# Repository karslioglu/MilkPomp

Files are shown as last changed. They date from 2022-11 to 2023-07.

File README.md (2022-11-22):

# Milk Pomp
Proje, kullanicinin farkli tip ve hacimli bardaklara makineden süt doldurmak için kullanilacak bir cihazin kontrol kartinin tasarlanmasi işidir.

Cihazın mekanik tasarımı, flow sensör ve pompa seçimi müşteri tarafından hazırlanmıştır. Bizim yapacağımız iş ise sistemin çalışmasını sağlayacak elektronik kontrol kartının tasarlanmasıdır.

## Sistemin Çalismasi
Cihaz maksimum 9 farklı bardak bilgisini hafızada tutabilir. Kullanıcı bardak seçimi yaparak kayıtlı bardak tiplerinden birini otomatik olarak doldurabilir. Fakat istenirse kayıtlı olmayan farklı bir kabı da manuel olarak istediği miktarda doldurabilir.

Cihaz üzerinde 3 adet buton ve 1 adet 7-Segment gösterge bulunmaktadır. Ayrıca, bir pulse girişi ile **Akış Sensoru** girişi okunacak ve çıkış olarak bir role kontrol edilecektir.

	* I/O (On/Off) butonu
	* Start butonu
	* Mode butonu
	* Akış Sensoru (Encoder Pulse Input)
	* Role
	
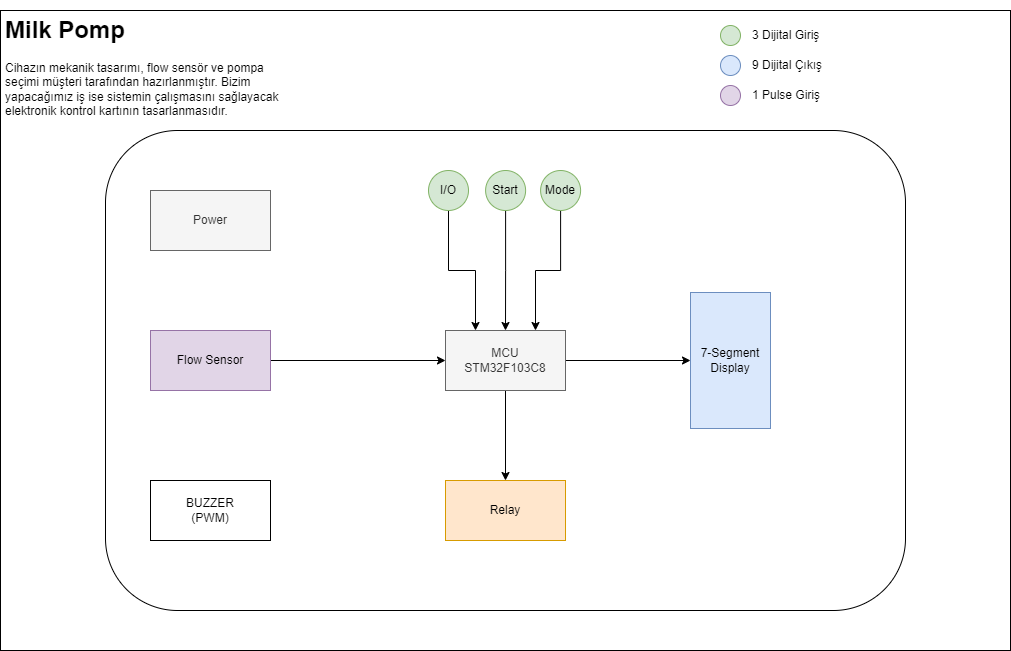
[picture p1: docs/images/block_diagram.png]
Block Diagram

	
Aşağıda tarif edilen çalışma şekilleri bu 3 buton ve gösterge kullanılarak gerçeklenecektir.

Sistemi çalıştırmak için I/O butonuna bir kere basıp bırakmak yeterlidir. Sistem kapalıyken gösterge ve diğer butonlar aktif değildir. I/O butonuna bir kere basılıp bırakıldığında sistem açılır, eğer kalibrasyon yapılmamışsa (hiç bardak tanımı yoksa) **C.** değeri görünür ve ekran yanıp söner. Aksi halde sabit olarak **0** yazar ve bardak seçimi için bekler.

Cihaz 3 farklı çalışma şekline sahip olacaktır.

### Kalibrasyon
Kalibrasyon modu, elimizde bulunan bardakların tanımlanması için kullanılır. Maksimum 9 farklı bardak tanımı yapılabilir.

Kalibrasyon modu bir adet bardak tanıtmak istenirse aşağıdaki algoritmaya göre çalışır

	1- Kalibrasyonu başlatmak için I/O butonuna 5 saniye basılı tutulur
	2- Gösterge 0 değerini gösterir ve nokta yanıp sönmeye başlar
	3- İstenilen bardak, cihazın bardak bölmesine yerleştirilir
	4- Mode butonu ile bardak seçimi yapılır (1, 2, 3, ..)
	5- Start butonuna basılı tutularak bardak doldurulur
	6- Bardak dolunca Start butonu bırakılır
	7- Start butonu bırakıldığında seçilen bardak ve doldurulan miktar bilgileri otomatik olarak kaydedilir
	8- Kalibrasyon modundan çıkmak için I/O butonuna 5 saniye bayunca basılır
	
Eğer birden fazla bardak tanımı yapılmak istenirse yukarıdaki algoritma basamaklarından 1 nolu adım ile kalibrasyon işlemi başlatılır. 2-7 adımları her bir bardak için tekrarlanır. Tüm bardakların tanımlanma işlemi bittiğinde 8 nolu adım ile kalibrasyon işlemi sonlandırılır.

Daha sonra tanımlı bir bardağın kalibrasyonu değiştirlmek istendiğinde veya yeni bir bardak tanımı yapılması gerektiğinde yukarıdaki algoritma tekrar uygulanabilir.

> Dikkat edilmesi gereken nokta, eğer bardak tanımları yapılmış bir cihazda tek bir bardağın kalibrasyonu değiştirlmek istenirse, Mode butonu ile doğru bardak numarasının seçildiğinden emin olunması gerekmektedir.

### Otomatik Mod
Kalibrasyonu yapılmış bir cihazda kullanıcı bardak seçimi yaparak tanımlı bardaklardan birini otomatik olarak doldurabilir.

	1- İstenilen bardak, cihazın bardak bölmesine yerleştirilir
	2- Mode butonu kullanılarak bardak seçimi yapılır
	3- Start butonuna basılıp bırakıldığında tanımlı miktar kadar dolum yapılır
	
Her bir bardak için yukarıdaki adımlar tekrarlanır.

### Manuel Mod
Kalibrasyon yapılarak tanımlanmamış bir bardak veya farklı bir kap doldurulmak istendiğinde Manuel mod kullanılır.

	1- Doldurulmak istenilen kap yerleştirilir.
	2- Start butonuna basılı tutulur. Butona basıldıktan 5 saniye sonra manuel dolum başlar
	3- Kullanıcı Start butonunu bıraktığında dolum işlemi sonlanır.

## Kullanilacak Bilesenler
[flow sensor](https://www.hepsiburada.com/fluidotech-kahve-makinasi-pompasi-rotary-pompa-pirinc-govdeli-p-HBV000007SB1Q)
[flow sensor kullanimi](https://how2electronics.com/iot-water-flow-meter-using-esp8266-water-flow-sensor/)
[ESP8266 with Water Flow Sensor](https://www.14core.com/wiring-esp8266-1212e-with-g12-liquid-water-flow-sensor-for-wireless-monitoring/)

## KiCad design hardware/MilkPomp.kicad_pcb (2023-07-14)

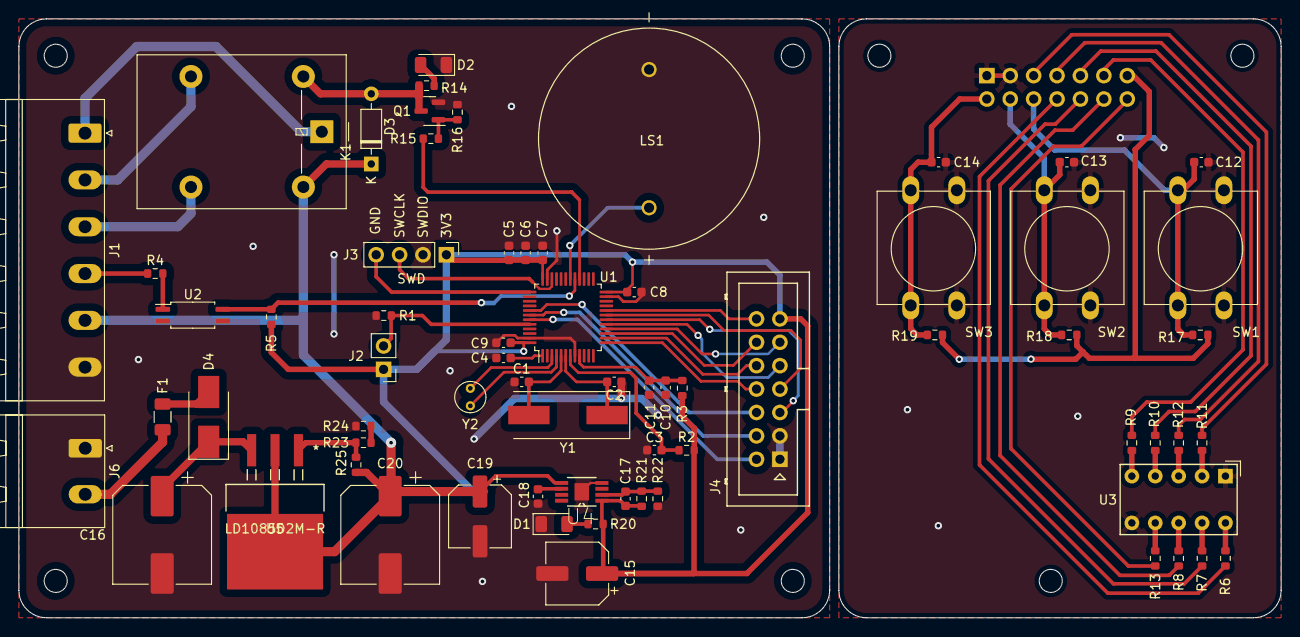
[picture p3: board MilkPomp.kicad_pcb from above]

Board: 2 copper layers, 137.0 x 65.0 mm, 76 parts (1 on the bottom side), 62 nets.

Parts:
C1, C2: 20pF; C_0603_1608Metric
C3, C5, C7, C8, C9, C10, C12, C13, C14: 100nF; C_0603_1608Metric
C4: 1uF/10V; C_0603_1608Metric
C6, C11: 1uF/6V; C_0603_1608Metric
C15: 10uF/10V; CP_Elec_6.3x7.7
C16, C20: 100uF/35V; CP_Elec_10x10.5
C17, C18: 10nF; C_0603_1608Metric
C19: 10uF/35V; CP_Elec_6.3x7.7
D1, D2: LED_GREEN; LED_1206_3216Metric
D3: 1N4148; D_DO-35_SOD27_P7.62mm_Horizontal
D4: SBR3A40SAQ; D_SMB_Handsoldering
F1: 1A; Fuse_1206_3216Metric
H1, H2, H3, H4, H5, H6, H7: MountingHole; MountingHole_2.5mm
J1: Screw_Terminal_01x06; PhoenixContact_MSTBA_2,5_6-G-5,08_1x06_P5.08mm_Horizontal
J2: BOOT; PinHeader_1x02_P2.54mm_Vertical
J3: Conn_01x04_Male; PinHeader_1x04_P2.54mm_Vertical
J4: Conn_Board; Multicomp_MC9A12-1434_2x07x2.54mm_Straight
J5: Conn_Display; Multicomp_MC9A12-1434_2x07x2.54mm_Straight
J6: PWR INPUT; PhoenixContact_MSTBA_2,5_2-G_1x02_P5.00mm_Horizontal
K1: G5LE-1; Relay_SPDT_Omron-G5LE-1
LS1: KPEG228; XDCR_KPEG228
Q1: BC847; SOT-23
R1, R2: 100K; R_0603_1608Metric
R3: 100R; R_0603_1608Metric
R4: 3K3; R_0603_1608Metric
R5, R14, R15: 4K7; R_0603_1608Metric
R6, R7, R8, R9, R10, R11, R12, R13: 330R; R_0603_1608Metric
R16: 47K; R_0603_1608Metric
R17, R18, R19, R22: 10K; R_0603_1608Metric
R20: 470; R_0603_1608Metric
R21: 18K; R_0603_1608Metric
R23: 1K; R_0603_1608Metric
R24: 33; R_0603_1608Metric
R25: 120; R_0603_1608Metric
SW1: SW_IO; SW_PUSH-12mm
SW2: SW_START; SW_PUSH-12mm
SW3: SW_MODE; SW_PUSH-12mm
U1: STM32F103C8Tx; LQFP-48_7x7mm_P0.5mm
U2: TLP291; SOIC-4_4.55x2.6mm_P1.27mm
U3: HDSP-7403; HDSP-7401
U4: TPS7A4901DGNT; SOP65P490X110-9N
U5: LD1085D2M-R
Y1: 8MHz; Crystal_SMD_HC49-SD
Y2: 32KHz; Crystal_C38-LF_D3.0mm_L8.0mm_Vertical

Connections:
+3V3: C5.1, C6.1, C7.1, C8.1, C9.1, C15.1, C17.1, J2.1, J3.1, J4.13, J5.13, R2.2, R3.1, R5.1, R17.1, R18.1, R19.1, R20.1, R21.1, U1.24 (VDD), U1.36 (VDD), U1.48 (VDD), U4.1 (OUT)
+12V: C19.1, C20.1, D3.1 (K), J1.5, K1.5, R25.1, U4.5 (EN), U4.8 (IN), U5.2 (OUTPUT), U5.4 (OUTPUT)
/Buttons/BTN_IO: C12.1, J5.6, R17.2, SW1.2
/Buttons/BTN_MODE: C14.1, J5.2, R19.2, SW3.2
/Buttons/BTN_START: C13.1, J5.4, R18.2, SW2.2
/DISPLAY/DISP_A: J5.8, R6.1
/DISPLAY/DISP_B: J5.10, R7.1
/DISPLAY/DISP_C: J5.12, R8.1
/DISPLAY/DISP_D: J5.11, R9.1
/DISPLAY/DISP_E: J5.9, R10.1
/DISPLAY/DISP_F: J5.5, R11.1
/DISPLAY/DISP_G: J5.7, R12.1
/DISPLAY/DISP_P: J5.14, R13.1
/Flow/FLOW_SENSOR: J1.4, R4.1
/Power/LED_PWR: D1.2 (A), R20.2
/Power/VCC: F1.2, J6.2
/Relay/RELAY_IN: J1.1, K1.1
/Relay/RELAY_NC: J1.3, K1.4
/Relay/RELAY_NO: J1.2, K1.3
BOOT0: J2.2, R1.1, U1.44 (BOOT0)
BTN_IO: J4.6, U1.41 (PB5)
BTN_MODE: J4.2, U1.43 (PB7)
BTN_START: J4.4, U1.42 (PB6)
BUZZER: LS1.P, U1.30 (PA9)
DISP_A: J4.8, U1.13 (PA3)
DISP_B: J4.10, U1.14 (PA4)
DISP_C: J4.12, U1.15 (PA5)
DISP_D: J4.11, U1.16 (PA6)
DISP_E: J4.9, U1.17 (PA7)
DISP_F: J4.5, U1.18 (PB0)
DISP_G: J4.7, U1.19 (PB1)
DISP_P: J4.14, U1.20 (PB2)
FLOW: R5.2, U1.29 (PA8), U2.4
GND: C1.1, C2.1, C3.2, C4.2, C5.2, C6.2, C7.2, C8.2, C9.2, C10.2, C11.2, C12.2, C13.2, C14.2, C15.2, C16.2, C18.2, C19.2, C20.2, D1.1 (K), D2.1 (K), J1.6, J3.2, J4.1, J4.3, J5.1, J5.3, J6.1, LS1.N, Q1.2 (E), R1.2, R16.2, R22.2, R24.2, SW1.1, SW2.1, SW3.1, U1.8 (VSSA), U1.23 (VSS), U1.35 (VSS), U1.47 (VSS), U2.2, U2.3, U3.1 (CC), U3.6 (CC), U4.4 (GND), U4.9 (THERMAL_PAD)
unnamed: C4.1, U1.1 (VBAT)
unnamed: C10.1, C11.1, R3.2, U1.9 (VDDA)
unnamed: C16.1, D4.1 (K), U5.3 (INPUTS)
unnamed: C17.2, R21.2, R22.1, U4.2 (FB)
unnamed: C18.1, U4.6 (NR/SS)
unnamed: D2.2 (A), R14.1
unnamed: D3.2 (A), K1.2, Q1.3 (C), R14.2
unnamed: D4.2 (A), F1.1
unnamed: Q1.1 (B), R15.2, R16.1
unnamed: R4.2, U2.1
unnamed: R6.2, U3.10 (A)
unnamed: R7.2, U3.9 (B)
unnamed: R8.2, U3.8 (C)
unnamed: R9.2, U3.5 (D)
unnamed: R10.2, U3.4 (E)
unnamed: R11.2, U3.2 (F)
unnamed: R12.2, U3.3 (G)
unnamed: R13.2, U3.7 (DP)
unnamed: R23.1, R25.2, U5.1 (ADJ)
unnamed: R23.2, R24.1
RCC_OSC32_IN: U1.3 (PC14), Y2.2
RCC_OSC32_OUT: U1.4 (PC15), Y2.1
RCC_OSC_IN: C1.2, U1.5 (PD0), Y1.2
RCC_OSC_OUT: C2.2, U1.6 (PD1), Y1.1
RELAY: R15.1, U1.28 (PB15)
SWCLK: J3.4, U1.37 (PA14)
SWDIO: J3.3, U1.34 (PA13)
nRESET: C3.1, R2.1, U1.7 (NRST)

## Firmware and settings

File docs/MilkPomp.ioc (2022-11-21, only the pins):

Mcu.UserName=STM32F103C8Tx
PA13.Signal=SYS_JTMS-SWDIO
PA14.Signal=SYS_JTCK-SWCLK
PA3.GPIO_Label=DISP_A
PA3.Signal=GPIO_Output
PA4.GPIO_Label=DISP_B
PA4.Signal=GPIO_Output
PA5.GPIO_Label=DISP_C
PA5.Signal=GPIO_Output
PA6.GPIO_Label=DISP_D
PA6.Signal=GPIO_Output
PA7.GPIO_Label=DISP_E
PA7.Signal=GPIO_Output
PA8.GPIO_Label=FLOW
PA8.Signal=S_TIM1_CH1
PA9.GPIO_Label=BUZZER
PA9.Signal=S_TIM1_CH2
PB0.GPIO_Label=DISP_F
PB0.Signal=GPIO_Output
PB1.GPIO_Label=DISP_G
PB1.Signal=GPIO_Output
PB15.GPIO_Label=RELAY
PB15.Signal=GPIO_Output
PB2.GPIO_Label=DISP_P
PB2.Signal=GPIO_Output
PB5.GPIO_Label=BTN_IO
PB5.Signal=GPXTI5
PB6.GPIO_Label=BTN_START
PB6.Signal=GPXTI6
PB7.GPIO_Label=BTN_MODE
PB7.Signal=GPXTI7
PC14-OSC32_IN.Signal=RCC_OSC32_IN
PC15-OSC32_OUT.Signal=RCC_OSC32_OUT
PD0-OSC_IN.Signal=RCC_OSC_IN
PD1-OSC_OUT.Signal=RCC_OSC_OUT

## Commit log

2022-11-01 Init repo
    [MilkPomp.kicad_pcb, MilkPomp.kicad_sch]
2022-11-07 Main page and MCU pace created
    [MilkPomp.kicad_sch, buttons.kicad_sch, display.kicad_sch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]
2022-11-21 Input buttons changed
2022-11-21 MCU module is completed
    [MilkPomp.kicad_sch, mcu.kicad_sch, power.kicad_sch]
2022-11-21 MCU SW fixed
    [mcu.kicad_sch]
2022-11-21 değişiklik yapıldı
    [MilkPomp.kicad_sch, buttons.kicad_sch]
2022-11-21 Buttons module completed by Utku CAM
    [MilkPomp.kicad_sch]
2022-11-21 Relay module completed
    [MilkPomp.kicad_sch, buttons.kicad_sch, power.kicad_sch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]
2022-11-21 Display circuit added
    [MilkPomp.kicad_sch, buttons.kicad_sch, display.kicad_sch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]
2022-11-22 flow sensor Flow sensor added to readme file
2022-11-22 ESP8266 with Water Flow Sensor added
2022-11-22 Flow module completed
    [MilkPomp.kicad_sch, buttons.kicad_sch, flow.kicad_sch]
2022-11-24 Schematics are completed
    [MilkPomp.kicad_pcb, MilkPomp.kicad_sch, buttons.kicad_sch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]
2022-11-25 milkpomp pcb continued
    [MilkPomp.kicad_pcb]
2022-11-29 PCB designed
    [MilkPomp.kicad_pcb, MilkPomp.kicad_sch, buttons.kicad_sch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]
2022-11-30 PCB designed2
    [MilkPomp.kicad_pcb]
2022-11-30 Footprints are assigned and Cut edges fixed
    [MilkPomp.kicad_pcb, MilkPomp.kicad_sch, buttons.kicad_sch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]
2022-11-30 PCB drawing completed
    [MilkPomp.kicad_pcb, MilkPomp.kicad_sch, mcu.kicad_sch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]
2022-12-01 All PCB drawing completed
    [MilkPomp.kicad_pcb]
2022-12-01 PCB design completed
    [MilkPomp.kicad_pcb, MilkPomp.kicad_sch, mcu.kicad_sch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]
2022-12-02 All PCB design completed
    [MilkPomp.kicad_pcb]
2023-07-14 yeni seyler eklendi
    [Buzzer_sch.kicad_sch, MilkPomp.kicad_pcb, MilkPomp.kicad_sch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]

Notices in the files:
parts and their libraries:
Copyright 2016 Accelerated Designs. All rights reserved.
